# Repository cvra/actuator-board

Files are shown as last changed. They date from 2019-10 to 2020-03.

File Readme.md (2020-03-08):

## CVRA Actuator Board

__Features:__

- STM32F302K8U6 (64K Flash, 16K RAM)
- IOs
    - 1 Digital input
    - 2 Analog input
    - 2 Servo PWM
    - 2 motor outputs for vacuum pump
- CAN interface with two 4pin Molex PicoBlade for daisy chaining
- Debug connector (7pin Molex PicoBlade)
    - SWD
    - UART

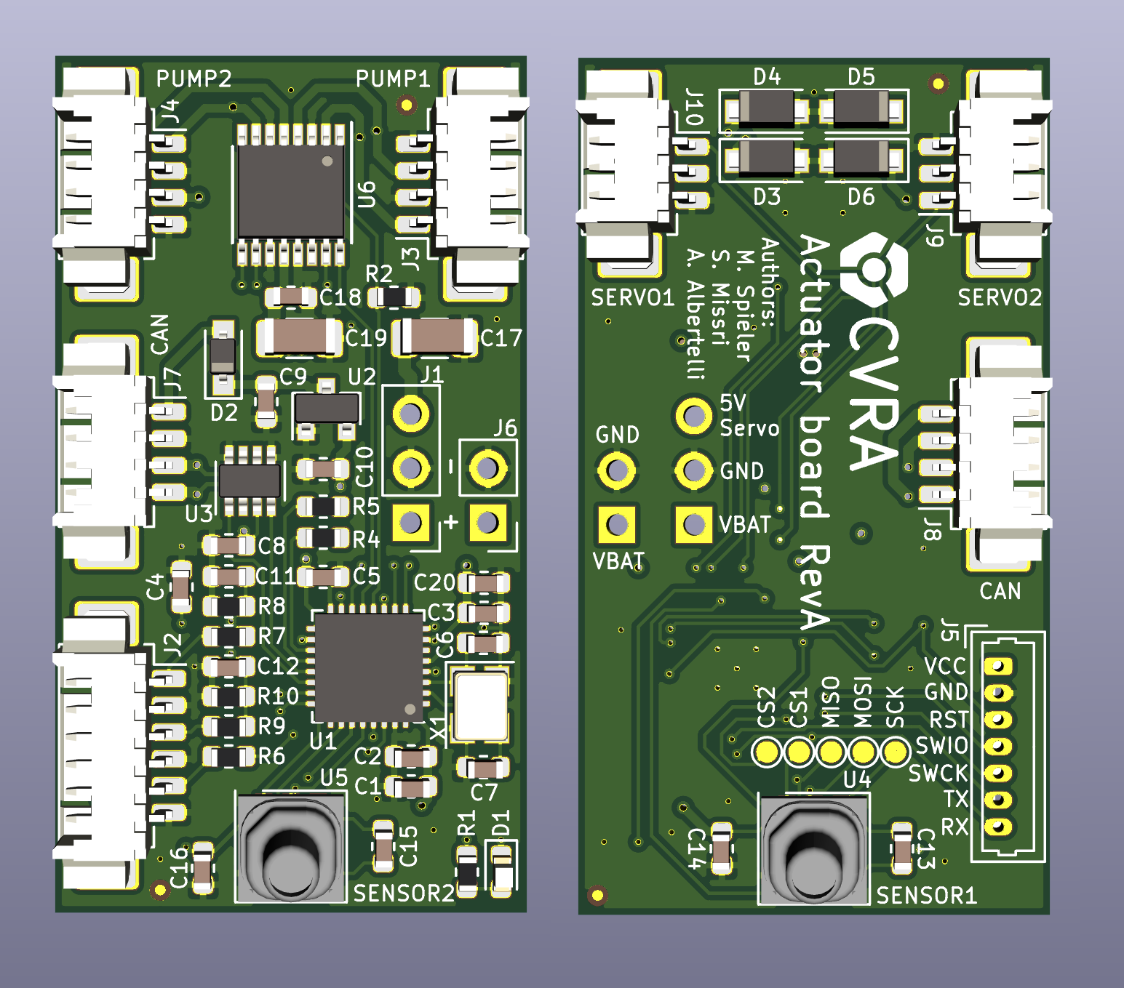
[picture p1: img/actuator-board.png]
Board Rendering

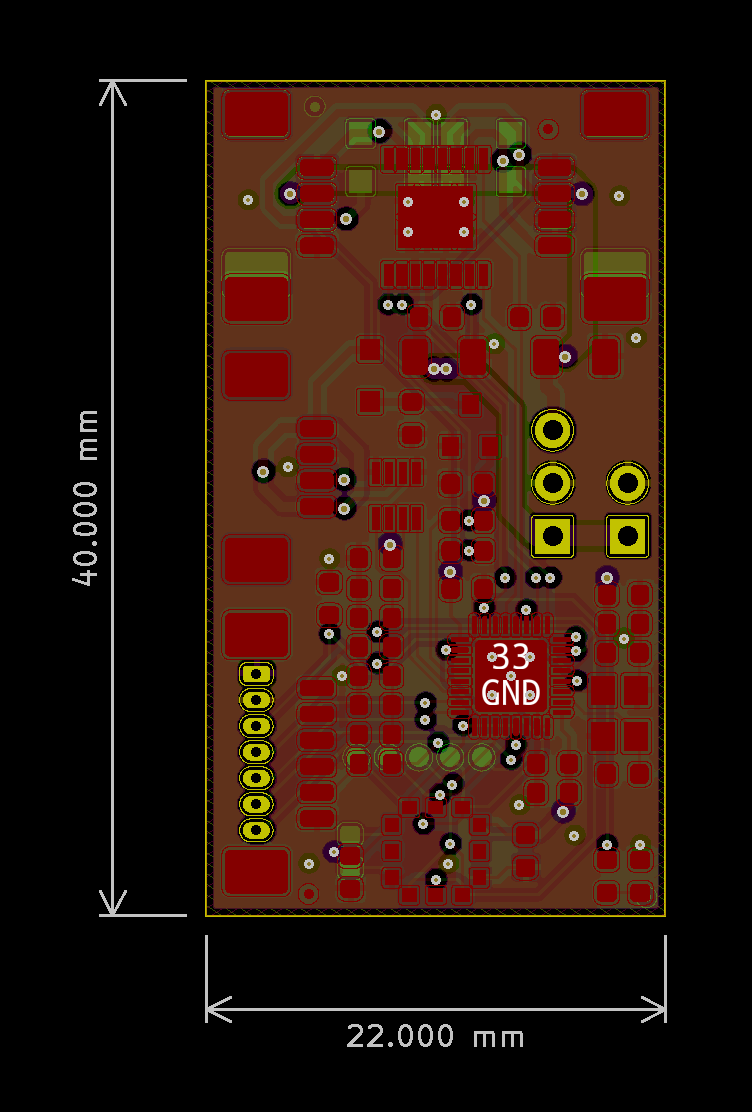
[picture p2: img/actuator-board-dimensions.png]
Board Dimensions


## Generating Digikey BOM using Kicost

Generate the Bom in XML format from KiCAD, then:

```
kicost -i actuator-board.xml --include digikey
```

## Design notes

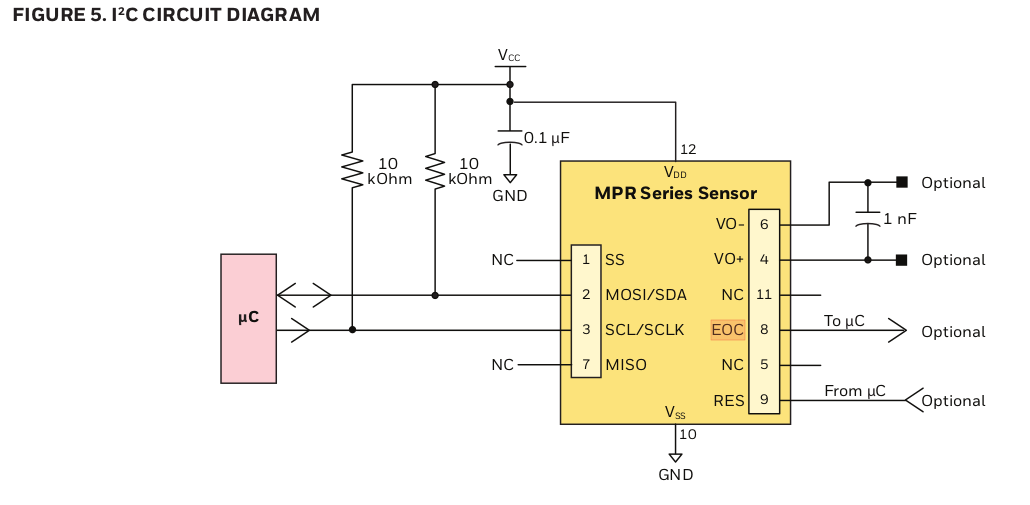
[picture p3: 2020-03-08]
doc/mprls_ref_design.png

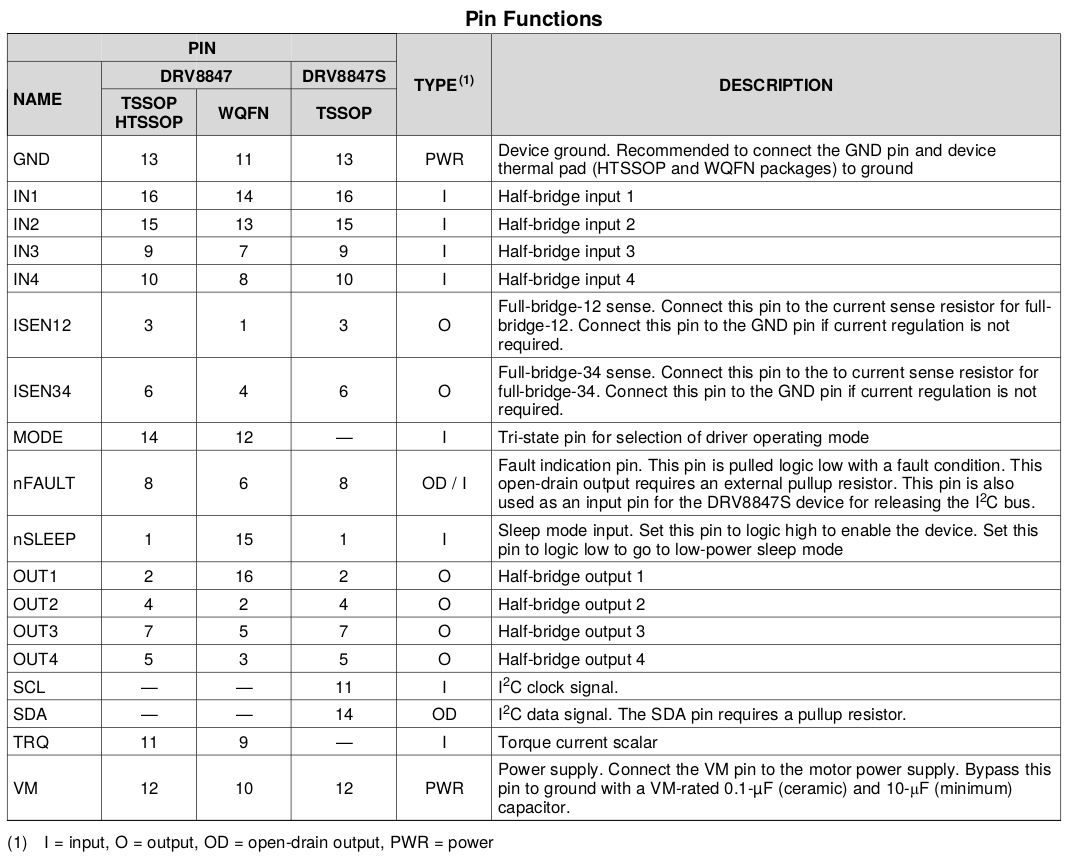
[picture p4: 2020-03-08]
doc/drv8847_pinout.png

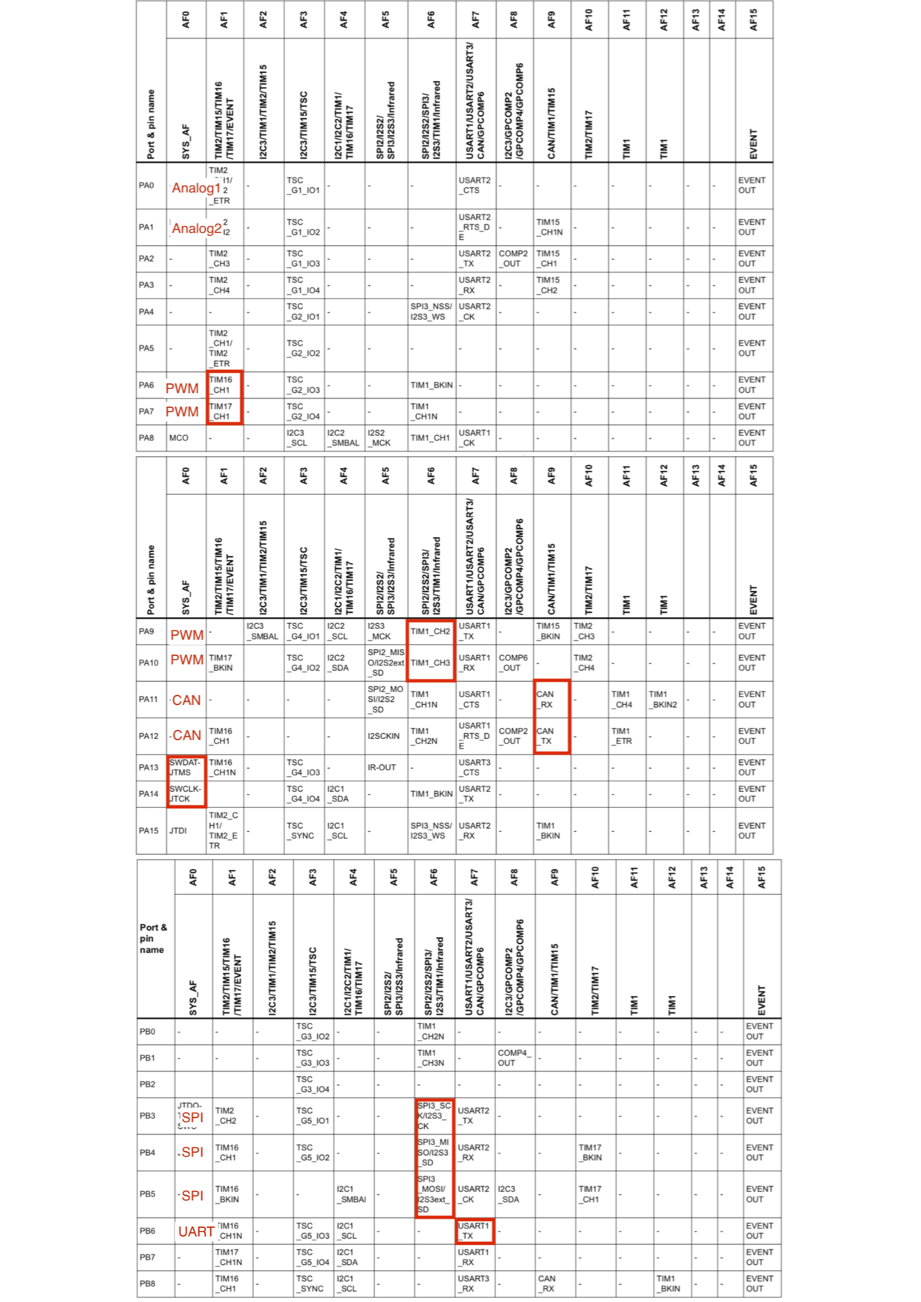
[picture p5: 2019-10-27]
doc/alternate_function.png

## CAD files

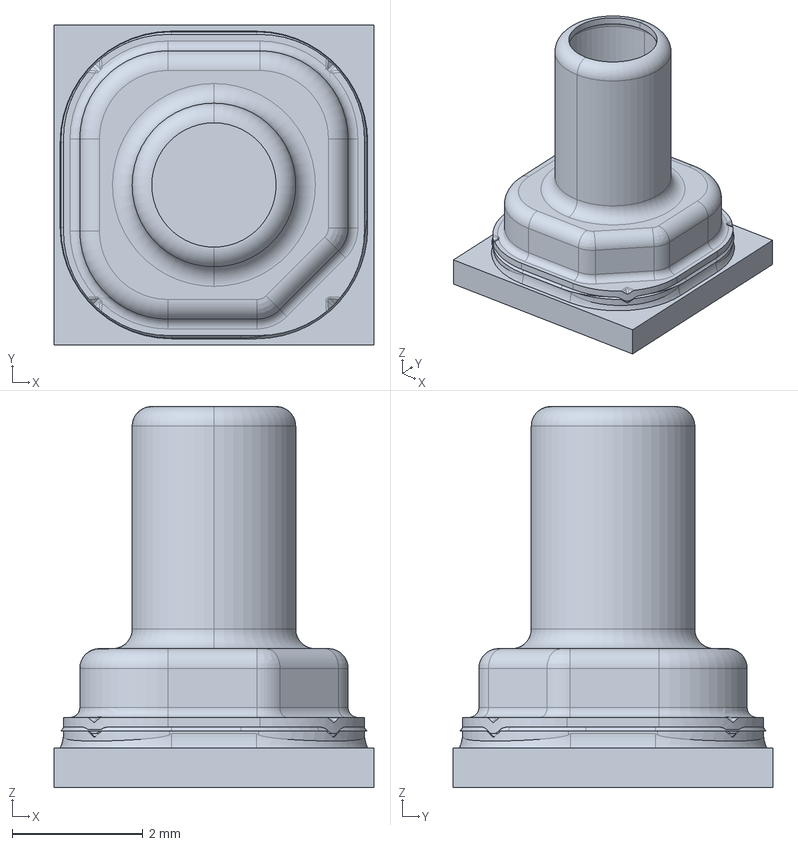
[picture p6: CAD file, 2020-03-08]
3dshapes/MPR.stp
4.89 x 4.89 x 5.82 mm

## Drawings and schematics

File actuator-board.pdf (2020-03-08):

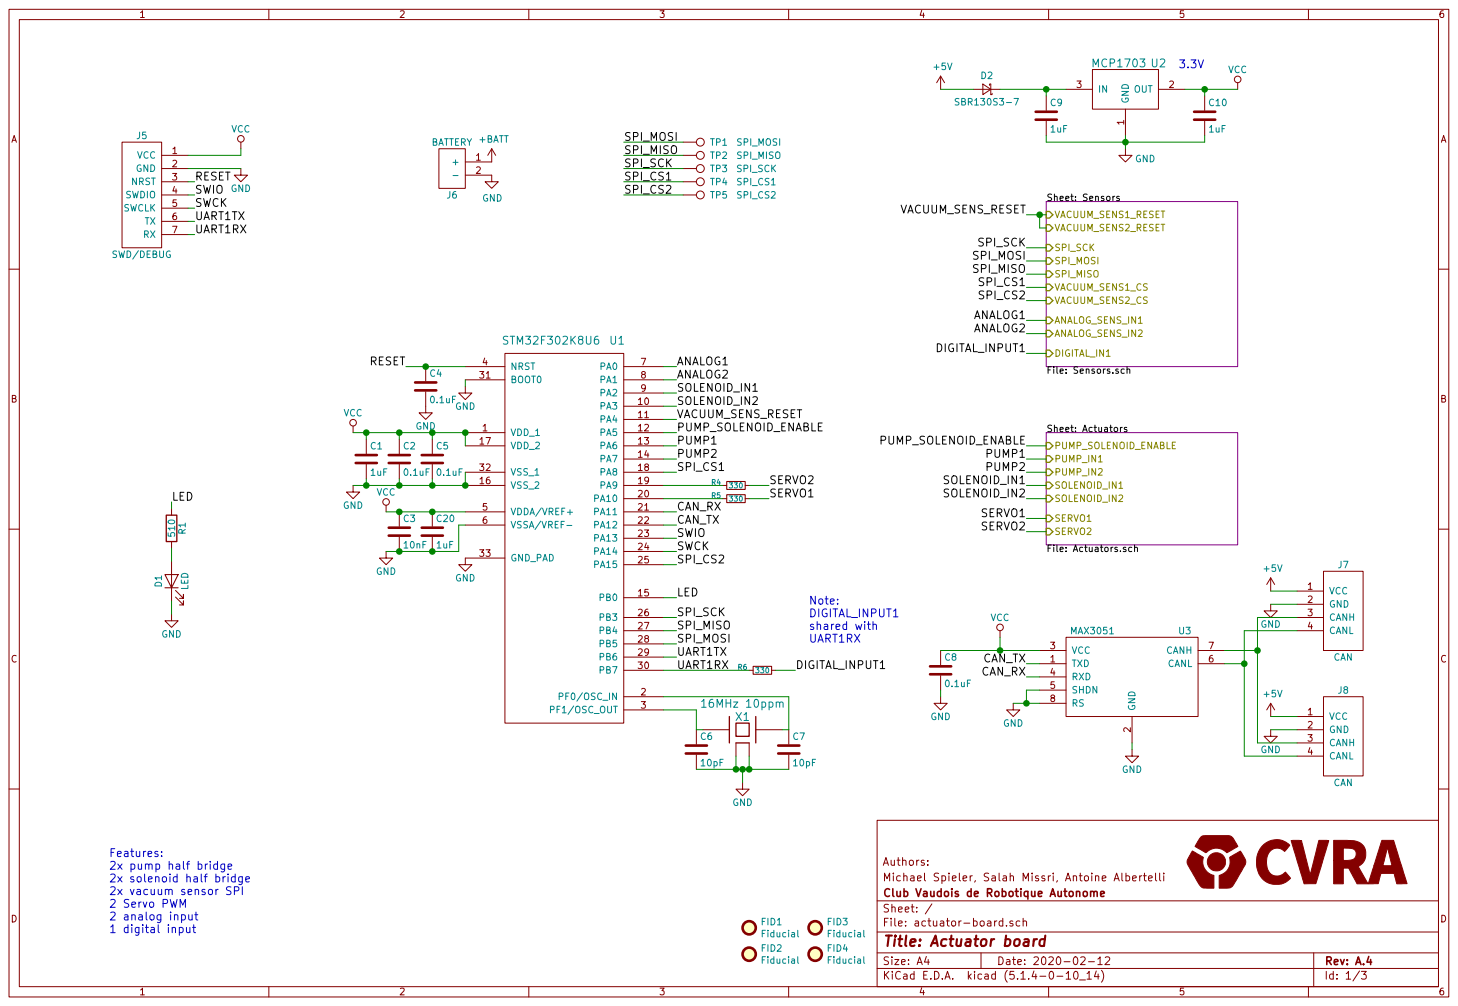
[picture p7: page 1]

SOLENOID_IN1 SOLENOID_IN2 Sheet: Sensors File: Sensors.sch VACUUM_SENS1_RESET ANALOG_SENS_IN1 ANALOG_SENS_IN2 DIGITAL_IN1 VACUUM_SENS2_RESET SPI_SCK

Sheet: Actuators File: Actuators.sch PUMP_IN1 PUMP_IN2 SERVO1 SERVO2 PUMP_SOLENOID_ENABLE

Features: 2x pump half bridge

Michael Spieler, Salah Missri, Antoine Albertelli Authors:

File: actuator-board.sch Sheet: / Club Vaudois de Robotique Autonome

Id: 1/3 Title: Actuator board

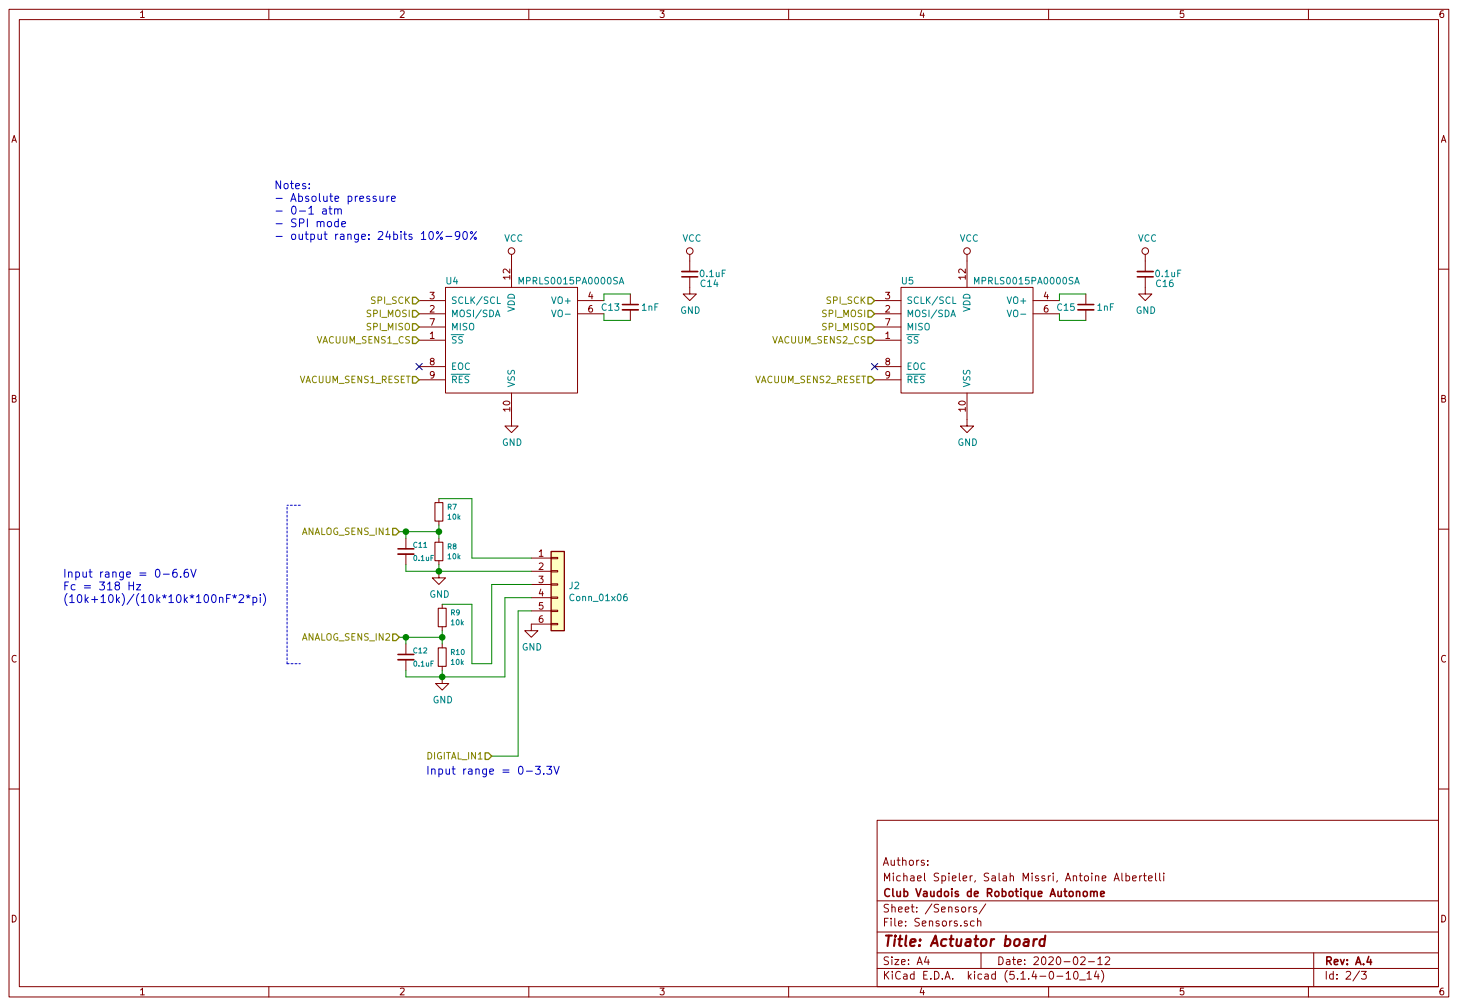
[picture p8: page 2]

File: Sensors.sch Sheet: /Sensors/ Club Vaudois de Robotique Autonome

Id: 2/3 Title: Actuator board

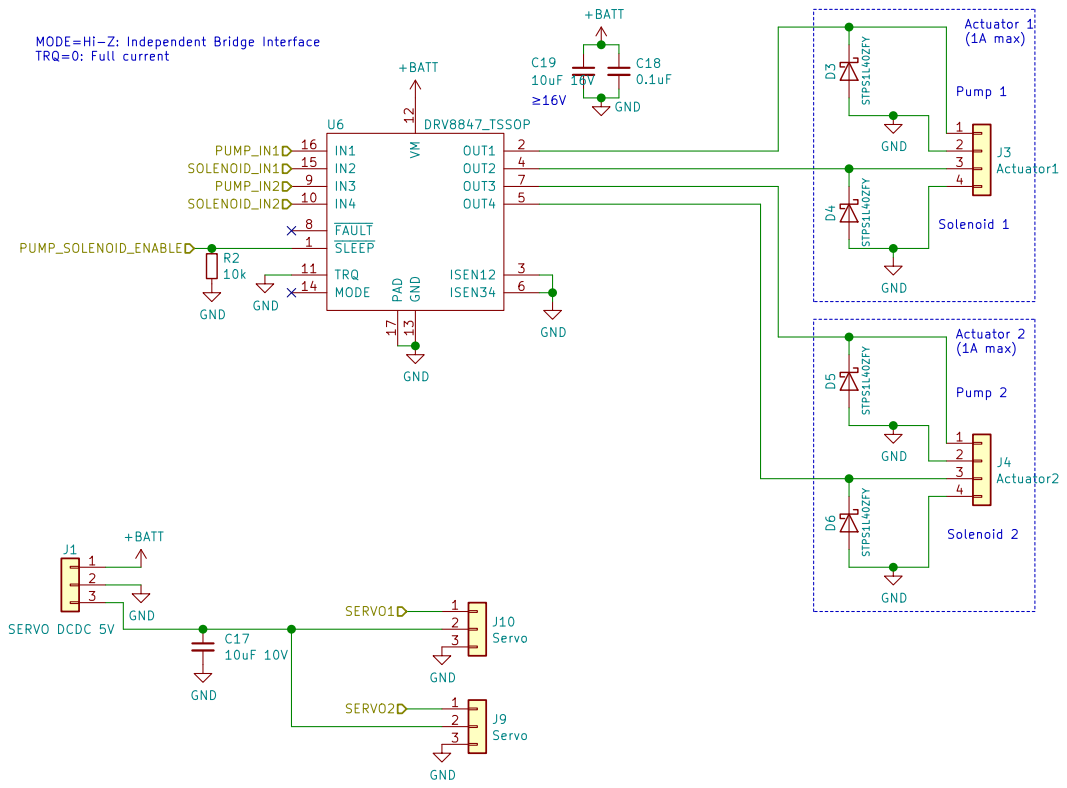
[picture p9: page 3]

File: Actuators.sch Sheet: /Actuators/ Club Vaudois de Robotique Autonome

Id: 3/3 Title: Actuator board

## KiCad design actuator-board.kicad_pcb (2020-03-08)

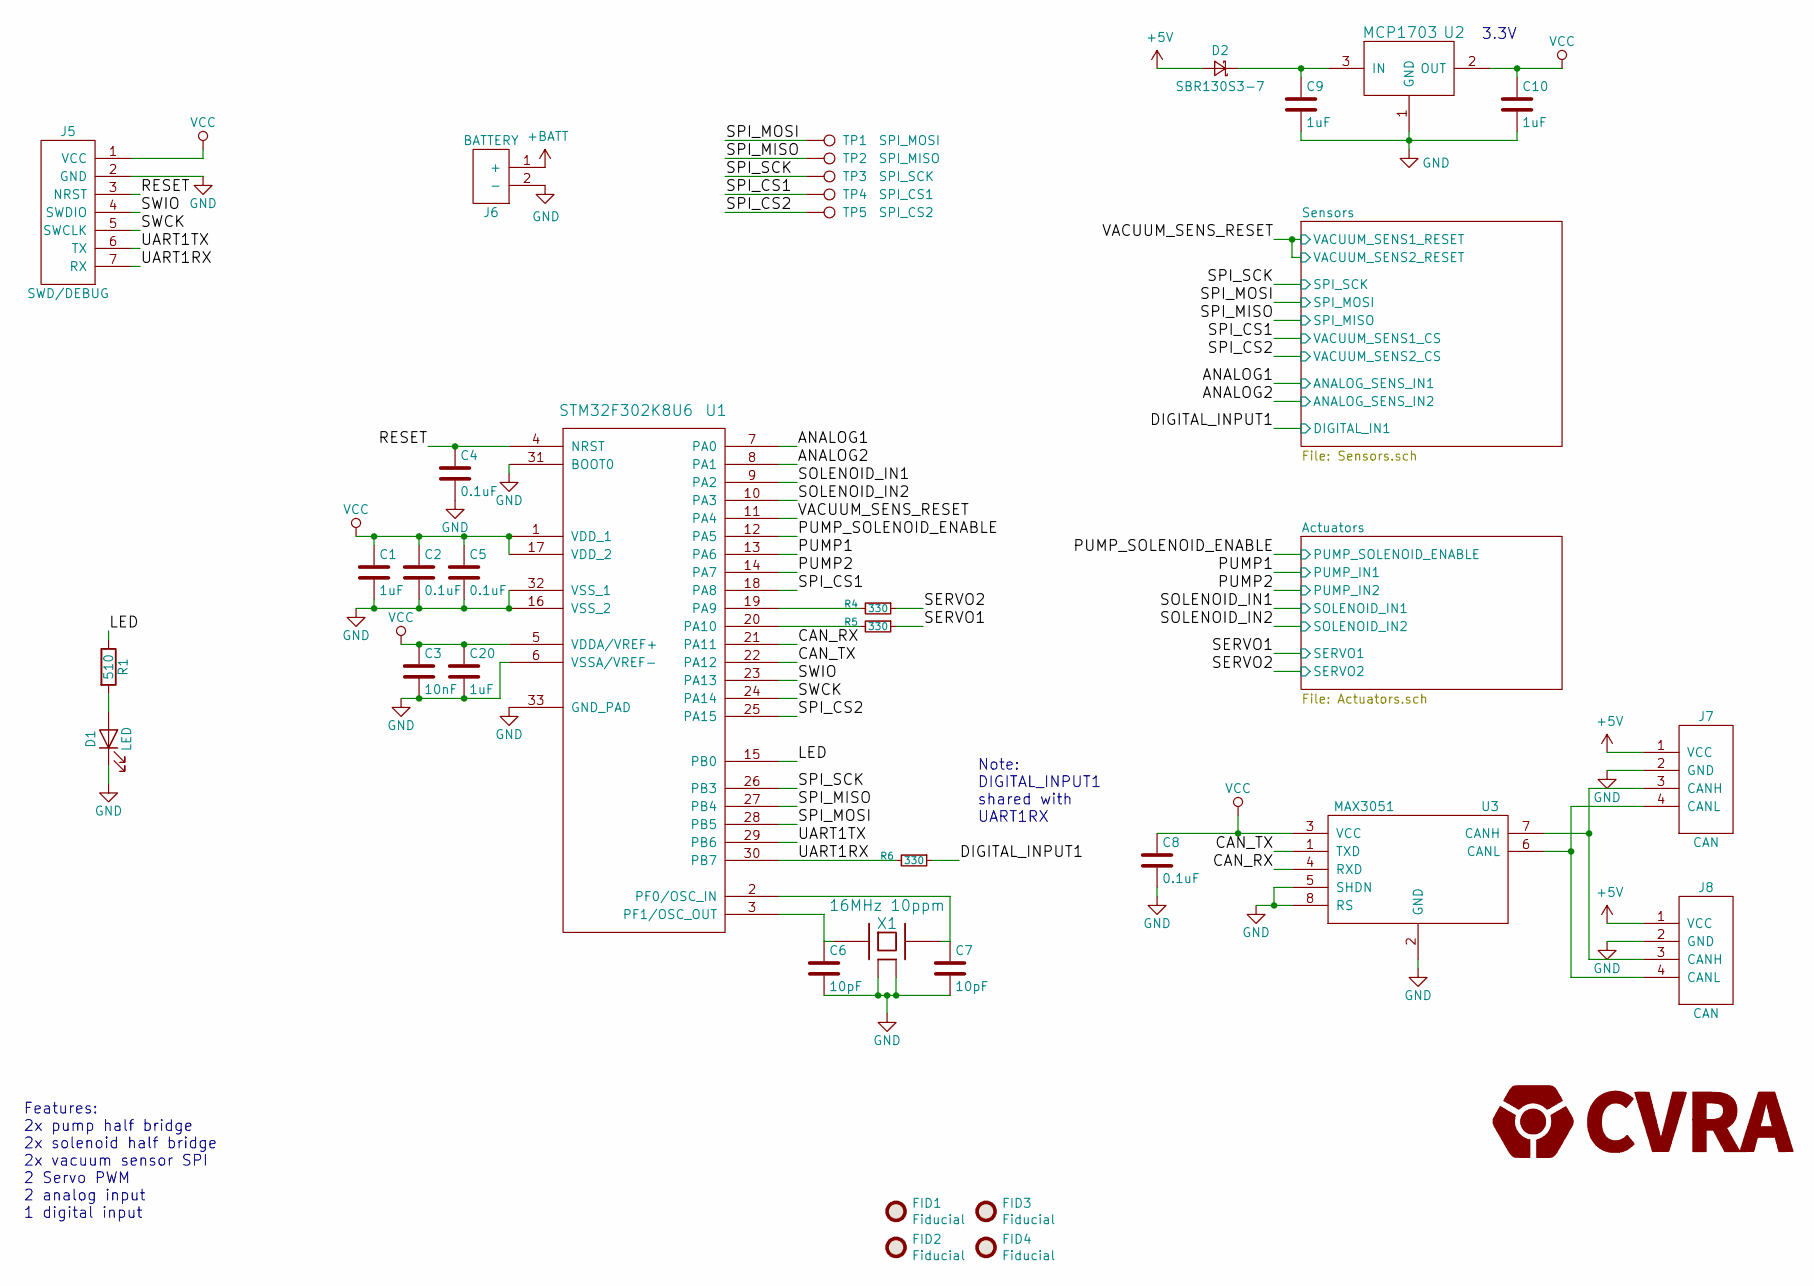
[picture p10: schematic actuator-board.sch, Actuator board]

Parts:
C1, C9, C10, C20: 1uF; C_0603_1608Metric; digikey# 399-3118-1-ND
C2, C4, C5, C8: 0.1uF; C_0603_1608Metric; digikey# 399-1283-1-ND
C3: 10nF; C_0603_1608Metric; digikey# 399-1092-1-ND
C6, C7: 10pF; C_0603_1608Metric; digikey# 399-17563-1-ND
D1: LED; LED_0603_1608Metric; digikey# VLMTG1300-GS08CT-ND
D2: SBR130S3-7; D_SOD-323_HandSoldering; digikey# SBR130S3-7DICT-ND
FID1, FID2, FID3, FID4: Fiducial; Fiducial_0.5mm_Mask1mm
J5: SWD/DEBUG; Molex_PicoBlade_53047-0710_1x07_P1.25mm_Vertical
J6: BATTERY; PinHeader_1x02_P2.54mm_Vertical
J7, J8: CAN; Molex_PicoBlade_53261-0471_1x04-1MP_P1.25mm_Horizontal; digikey# WM7622CT-ND
R1: 510; R_0603_1608Metric; digikey# 311-510GRCT-ND
R4, R5, R6: 330; R_0603_1608Metric; digikey# 311-330HRCT-ND
TP1: SPI_MOSI; TestPoint_Pad_D1.0mm
TP2: SPI_MISO; TestPoint_Pad_D1.0mm
TP3: SPI_SCK; TestPoint_Pad_D1.0mm
TP4: SPI_CS1; TestPoint_Pad_D1.0mm
TP5: SPI_CS2; TestPoint_Pad_D1.0mm
U1: STM32F302K8U6; QFN-32-1EP_5x5mm_P0.5mm_EP3.45x3.45mm; digikey# 497-14700-ND
U2: MCP1703; SOT-23; digikey# MCP1703T-3302E/CBCT-ND
U3: MAX3051; SOT-23-8; digikey# MAX3051EKA+TCT-ND
X1: 16MHz 10ppm; Crystal_SMD_SeikoEpson_TSX3225-4Pin_3.2x2.5mm; digikey# SER4069CT-ND

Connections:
+5V: D2.2 (A), J7.1 (VCC), J8.1 (VCC)
+BATT: J6.1 (+); also elsewhere on the board
/ANALOG1: U1.7 (PA0); also elsewhere on the board
/ANALOG2: U1.8 (PA1); also elsewhere on the board
/CAN_RX: U1.21 (PA11), U3.4 (RXD)
/CAN_TX: U1.22 (PA12), U3.1 (TXD)
/DIGITAL_INPUT1: R6.1; also elsewhere on the board
/LED: R1.1, U1.15 (PB0)
/PUMP1: U1.13 (PA6); also elsewhere on the board
/PUMP2: U1.14 (PA7); also elsewhere on the board
/PUMP_SOLENOID_ENABLE: U1.12 (PA5); also elsewhere on the board
/RESET: C4.1, J5.3 (NRST), U1.4 (NRST)
/SERVO1: R5.1; also elsewhere on the board
/SERVO2: R4.1; also elsewhere on the board
/SOLENOID_IN1: U1.9 (PA2); also elsewhere on the board
/SOLENOID_IN2: U1.10 (PA3); also elsewhere on the board
/SPI_CS1: TP4.1, U1.18 (PA8); also elsewhere on the board
/SPI_CS2: TP5.1, U1.25 (PA15); also elsewhere on the board
/SPI_MISO: TP2.1, U1.27 (PB4); also elsewhere on the board
/SPI_MOSI: TP1.1, U1.28 (PB5); also elsewhere on the board
/SPI_SCK: TP3.1, U1.26 (PB3); also elsewhere on the board
/SWCK: J5.5 (SWCLK), U1.24 (PA14)
/SWIO: J5.4 (SWDIO), U1.23 (PA13)
/UART1RX: J5.7 (RX), R6.2, U1.30 (PB7)
/UART1TX: J5.6 (TX), U1.29 (PB6)
/VACUUM_SENS_RESET: U1.11 (PA4); also elsewhere on the board
GND: C1.2, C2.2, C3.2, C4.2, C5.2, C6.2, C7.2, C8.2, C9.2, C10.2, C20.2, D1.1 (K), J5.2 (GND), J6.2 (-), J7.2 (GND), J8.2 (GND), U1.6 (VSSA/VREF-), U1.16 (VSS_2), U1.31 (BOOT0), U1.32 (VSS_1), U1.33 (GND_PAD), U2.1 (GND), U3.2 (GND), U3.5 (SHDN), U3.8 (RS), X1.2 (case), X1.4 (case); also elsewhere on the board
unnamed: C6.1, U1.3 (PF1/OSC_OUT), X1.1
unnamed: C7.1, U1.2 (PF0/OSC_IN), X1.3
unnamed: C9.1, D2.1 (K), U2.3 (IN)
unnamed: D1.2 (A), R1.2
unnamed: J7.3 (CANH), J8.3 (CANH), U3.7 (CANH)
unnamed: J7.4 (CANL), J8.4 (CANL), U3.6 (CANL)
unnamed: R4.2, U1.19 (PA9)
unnamed: R5.2, U1.20 (PA10)
VCC: C1.1, C2.1, C3.1, C5.1, C8.1, C10.1, C20.1, J5.1 (VCC), U1.1 (VDD_1), U1.5 (VDDA/VREF+), U1.17 (VDD_2), U2.2 (OUT), U3.3 (VCC); also elsewhere on the board

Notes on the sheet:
Features: 2x pump half bridge 2x solenoid half bridge 2x vacuum sensor SPI 2 Servo PWM 2 analog input 1 digital input
3.3V
Note: DIGITAL_INPUT1 shared with UART1RX

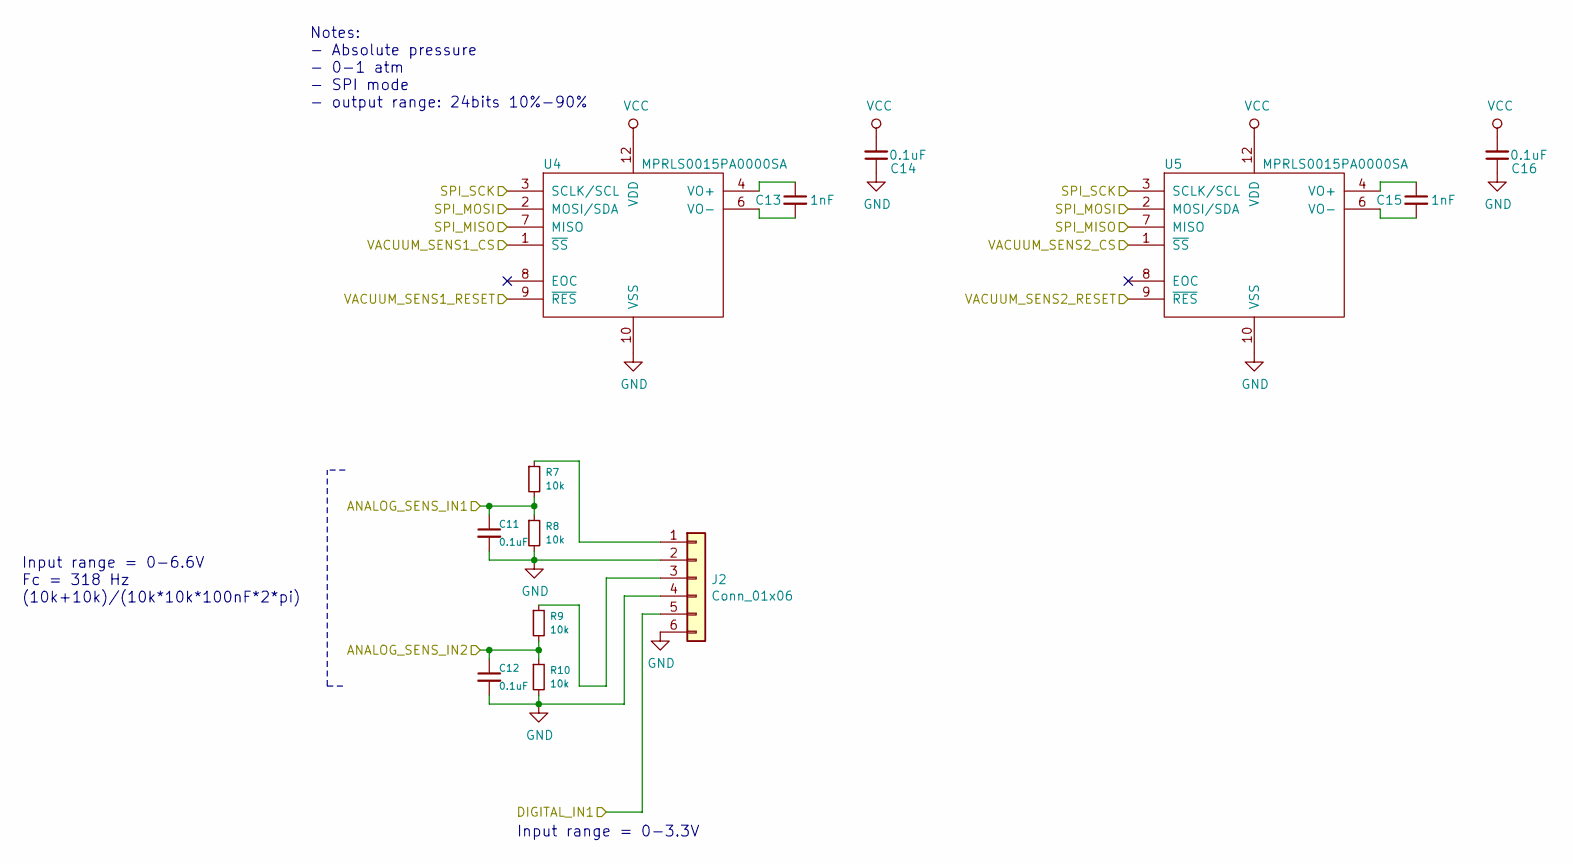
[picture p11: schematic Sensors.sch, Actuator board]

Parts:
C11, C12, C14, C16: 0.1uF; C_0603_1608Metric; digikey# 399-1283-1-ND
C13, C15: 1nF; C_0603_1608Metric; digikey# 399-8984-1-ND
J2: Conn_01x06; Molex_PicoBlade_53261-0671_1x06-1MP_P1.25mm_Horizontal; digikey# WM7626CT-ND
R7, R8, R9, R10: 10k; R_0603_1608Metric; digikey# 311-10KGRCT-ND
U4, U5: MPRLS0015PA0000SA; MPR-AbsoluteRef; digikey# 480-7099-1-ND

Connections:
/ANALOG1: C11.1, R7.2, R8.1; also elsewhere on the board
/ANALOG2: C12.1, R9.2, R10.1; also elsewhere on the board
/DIGITAL_INPUT1: J2.5; also elsewhere on the board
/SPI_CS1: U4.1 (~SS); also elsewhere on the board
/SPI_CS2: U5.1 (~SS); also elsewhere on the board
/SPI_MISO: U4.7 (MISO), U5.7 (MISO); also elsewhere on the board
/SPI_MOSI: U4.2 (MOSI/SDA), U5.2 (MOSI/SDA); also elsewhere on the board
/SPI_SCK: U4.3 (SCLK/SCL), U5.3 (SCLK/SCL); also elsewhere on the board
/VACUUM_SENS_RESET: U4.9 (~RES), U5.9 (~RES); also elsewhere on the board
GND: C11.2, C12.2, C14.1, C16.1, J2.2, J2.4, J2.6, R8.2, R10.2, U4.10 (VSS), U5.10 (VSS); also elsewhere on the board
unnamed: C13.1, U4.4 (VO+)
unnamed: C13.2, U4.6 (VO-)
unnamed: C15.1, U5.4 (VO+)
unnamed: C15.2, U5.6 (VO-)
unnamed: J2.1, R7.1
unnamed: J2.3, R9.1
VCC: C14.2, C16.2, U4.12 (VDD), U5.12 (VDD); also elsewhere on the board

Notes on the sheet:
Notes: - Absolute pressure - 0-1 atm - SPI mode - output range: 24bits 10%-90%
Input range = 0-6.6V Fc = 318 Hz (10k+10k)/(10k*10k*100nF*2*pi)
Input range = 0-3.3V

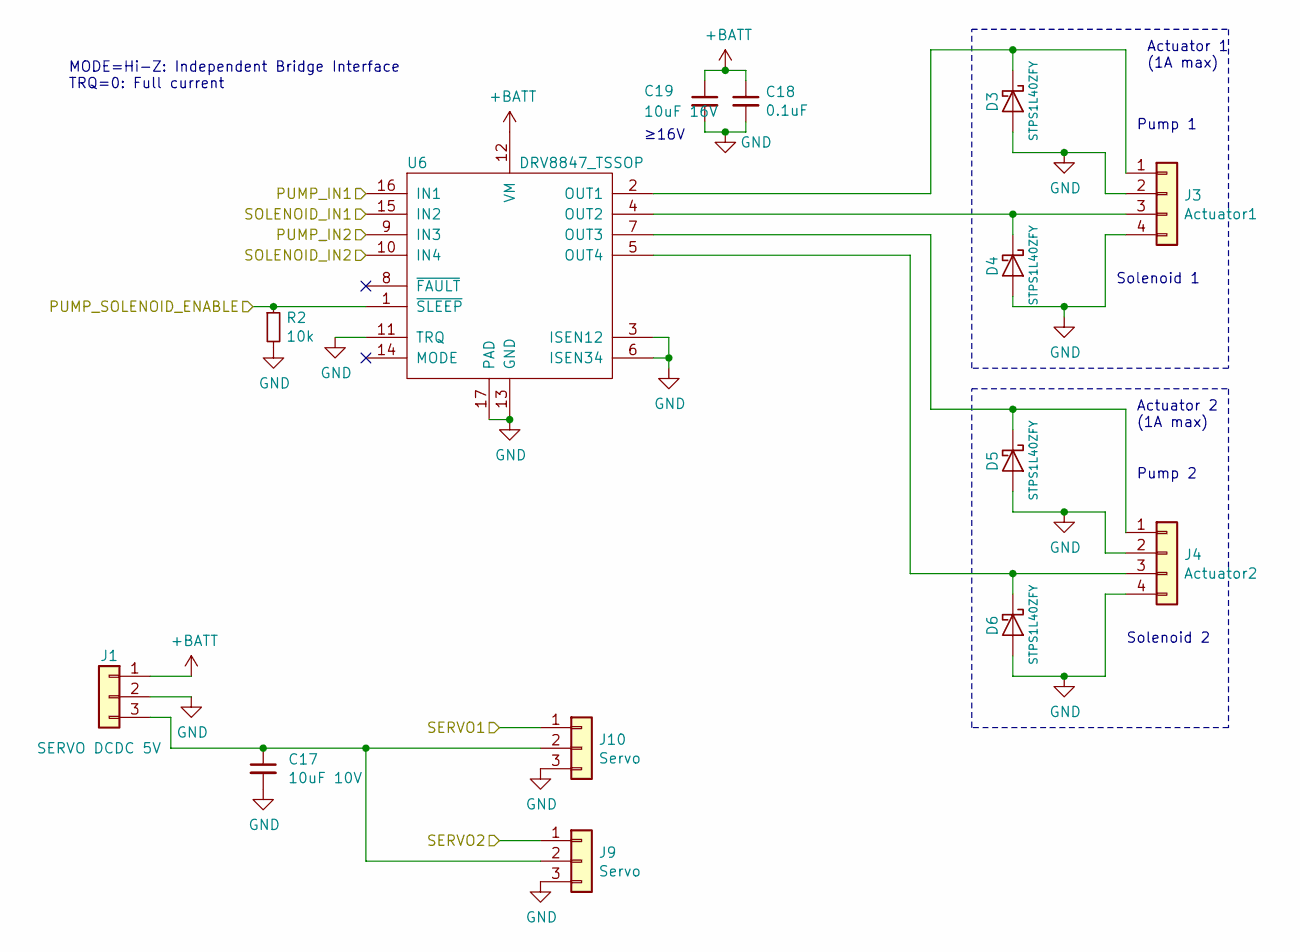
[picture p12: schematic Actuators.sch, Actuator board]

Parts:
C17: 10uF 10V; C_1206_3216Metric; digikey# 399-8155-1-ND
C18: 0.1uF; C_0603_1608Metric; digikey# 399-1283-1-ND
C19: 10uF 16V; C_1206_3216Metric; digikey# 399-7442-1-ND
D3, D4, D5, D6: STPS1L40ZFY; D_SOD-123F; digikey# 497-17153-1-ND
J1: SERVO DCDC 5V; PinHeader_1x03_P2.54mm_Vertical
J3: Actuator1; Molex_PicoBlade_53261-0471_1x04-1MP_P1.25mm_Horizontal; digikey# WM7622CT-ND
J4: Actuator2; Molex_PicoBlade_53261-0471_1x04-1MP_P1.25mm_Horizontal; digikey# WM7622CT-ND
J9, J10: Servo; Molex_PicoBlade_53261-0371_1x03-1MP_P1.25mm_Horizontal; digikey# WM7621CT-ND
R2: 10k; R_0603_1608Metric; digikey# 311-10KGRCT-ND
U6: DRV8847_TSSOP; TSSOP-16-1EP_4.4x5mm_P0.65mm; digikey# 296-53424-1-ND

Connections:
+BATT: C18.1, C19.1, J1.1, U6.12 (VM); also elsewhere on the board
/PUMP1: U6.16 (IN1); also elsewhere on the board
/PUMP2: U6.9 (IN3); also elsewhere on the board
/PUMP_SOLENOID_ENABLE: R2.1, U6.1 (~SLEEP); also elsewhere on the board
/SERVO1: J10.1; also elsewhere on the board
/SERVO2: J9.1; also elsewhere on the board
/SOLENOID_IN1: U6.15 (IN2); also elsewhere on the board
/SOLENOID_IN2: U6.10 (IN4); also elsewhere on the board
GND: C17.2, C18.2, C19.2, D3.2 (A), D4.2 (A), D5.2 (A), D6.2 (A), J1.2, J3.2, J3.4, J4.2, J4.4, J9.3, J10.3, R2.2, U6.3 (ISEN12), U6.6 (ISEN34), U6.11 (TRQ), U6.13 (GND), U6.17 (PAD); also elsewhere on the board
unnamed: C17.1, J1.3, J9.2, J10.2
unnamed: D3.1 (K), J3.1, U6.2 (OUT1)
unnamed: D4.1 (K), J3.3, U6.4 (OUT2)
unnamed: D5.1 (K), J4.1, U6.7 (OUT3)
unnamed: D6.1 (K), J4.3, U6.5 (OUT4)

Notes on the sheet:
Actuator 1 (1A max)
Actuator 2 (1A max)
MODE=Hi-Z: Independent Bridge Interface TRQ=0: Full current
≥16V
Pump 2
Solenoid 2
Solenoid 1
Pump 1

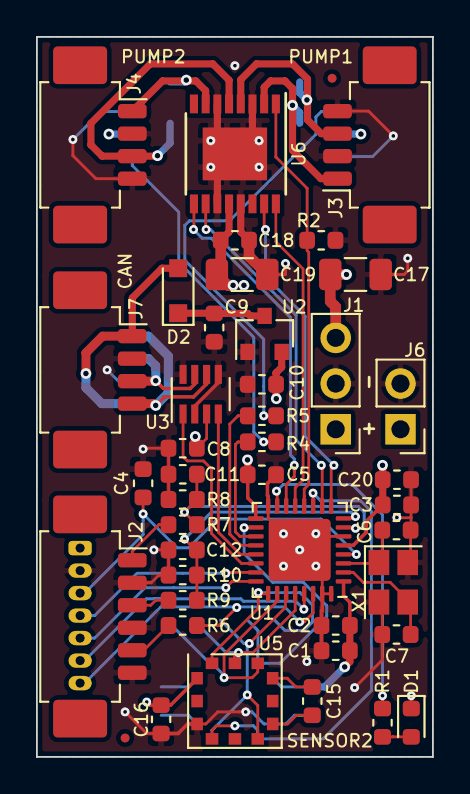
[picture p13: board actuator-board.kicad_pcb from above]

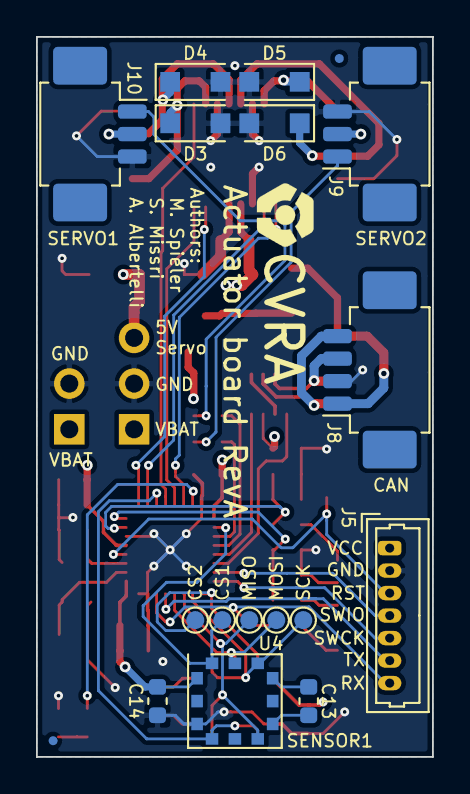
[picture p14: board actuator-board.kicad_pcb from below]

Board: 4 copper layers, 22.0 x 40.0 mm, 62 parts (19 on the bottom side), 47 nets.

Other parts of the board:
G1: LOGO; CVRA-logo-small

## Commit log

2016-03-09 schematic & component placement
    [can-io-board.kicad_pcb, can-io-board.sch]
2016-03-09 pcb rules
    [can-io-board.kicad_pcb]
2016-03-10 routing done
    [can-io-board.kicad_pcb, can-io-board.sch]
2016-03-10 add pdf schematic
2016-03-10 Set GND pad clearance and width
    [can-io-board.kicad_pcb]
2016-03-10 Hide component references in silkscreen
    [can-io-board.kicad_pcb]
2016-03-10 Improve VCC routing
    [can-io-board.kicad_pcb]
2016-03-10 Flip debug connector
    [can-io-board.kicad_pcb]
2016-03-10 nicer tracks
    [can-io-board.kicad_pcb]
2016-03-10 Improve GND connection
    [can-io-board.kicad_pcb]
2016-03-10 Remove silkscreen
    [can-io-board.kicad_pcb]
2016-03-10 add gerber
    [can-io-board-B.Cu.gbl, can-io-board-B.Paste.gbp, can-io-board-B.SilkS.gbo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]
2016-03-10 fix pin name, add silkscreen
    [can-io-board.kicad_pcb, can-io-board.sch]
2016-03-10 add final gerber
    [can-io-board-B.Cu.gbl, can-io-board-B.Mask.gbs, can-io-board-B.SilkS.gbo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]
2016-03-10 track fp lib table
2016-03-10 optimize C9 connection
    [can-io-board-B.Cu.gbl, can-io-board-B.Mask.gbs, can-io-board-B.Paste.gbp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]
2016-03-11 add pcb preview
2016-03-27 oscillator reference
    [can-io-board.sch]
2018-10-17 Start layout on RevB
    [can-io-board.kicad_pcb, can-io-board.sch]
2018-10-17 CAN connector on opposite sides
    [can-io-board.kicad_pcb]
2018-10-18 Reduced number of IO, use PicoBlade connector
    [can-io-board.kicad_pcb, can-io-board.sch]
2018-10-19 Routing almost finished
    [can-io-board.kicad_pcb, can-io-board.sch]
2018-10-19 fix DRC
    [can-io-board.kicad_pcb]
2018-10-19 Capacitor spacing
    [can-io-board.kicad_pcb]
2018-10-24 Improved GND connection, solder mask clearance
    [can-io-board.kicad_pcb]
2018-10-25 Silkscreen placement
    [can-io-board.kicad_pcb, can-io-board.sch]
2018-10-25 Add Digikey ref in schematic, add BOM
    [bom.csv, can-io-board.sch]
2018-10-28 Add CAN reverse voltage protection diode
    [bom.csv, can-io-board.kicad_pcb, can-io-board.sch]
2018-10-28 Plot schematic, move RevA to subfolder
    [can-io-board-B.Cu.gbl, can-io-board-B.Mask.gbs, can-io-board-B.Paste.gbp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]
2018-10-28 Solder paste clearance -10%
    [can-io-board.kicad_pcb]
2018-10-28 Gerber file export
    [can-io-board-B.Cu.gbl, can-io-board-B.Mask.gbs, can-io-board-B.Paste.gbp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]
2019-10-25 Start actuator-board
    [actuator-board.sch, bom.csv, can-io-board.kicad_pcb]
2019-10-25 remove CAN-IO stuff
    [can-io-board-B.Cu.gbl, can-io-board-B.Mask.gbs, can-io-board-B.Paste.gbp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]
2019-10-26 pin assignment WIP
    [actuator-board.sch]
2020-01-18 Ignore kicad backups and PDFs
2020-01-18 Add components for half bridges and vaccuum sensor
2020-01-18 Finish the design of th actuator board schematic
    [Actuators.sch, Sensors.sch, actuator-board.sch]
2020-01-25 Correct schematics after review
    [Actuators.sch, Sensors.sch, actuator-board.sch]
2020-02-02 Cleanup labels, motor placement, power labels
    [Actuators.sch, Sensors.sch, actuator-board.sch]
2020-02-02 Change to Schottky flyback diode, update valve symbol
    [Actuators.sch, actuator-board.sch]
2020-02-02 Clear component annotation
    [Actuators.sch, Sensors.sch, actuator-board.sch]
2020-02-06 updated kicad lib symbols
2020-02-06 Switch to SPI, fixed sensor and motor driver symbols.
    [Actuators.sch, Sensors.sch, actuator-board.sch]
2020-02-08 Work on footprint assignment
    [Actuators.sch, Sensors.sch, actuator-board.sch]
2020-02-12 Review update
    [Actuators.sch, Sensors.sch, actuator-board.sch]
2020-02-12 Input range note, rough footprint assignment
    [Actuators.sch, Sensors.sch, actuator-board.sch]
2020-02-12 Create PCB file, import footprints, rough arrangement
    [actuator-board.kicad_pcb]
2020-02-13 Upadate footprints, rough arrangement
    [Actuators.sch, Sensors.sch, actuator-board.kicad_pcb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]
2020-02-13 Add digikey references for BOM
    [Actuators.sch, Sensors.sch, actuator-board.sch]
2020-02-13 Rough component placement, defined outline
    [actuator-board.kicad_pcb]
2020-02-16 Update footprints, better refdes, cleanup schematic, 40x22mm outline
    [Actuators.sch, Sensors.sch, actuator-board.kicad_pcb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]
2020-02-16 Update authors, DRC rules, layers, track/via settings
    [Actuators.sch, Sensors.sch, actuator-board.kicad_pcb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]
2020-02-20 Sensor/gpio/debug routing
    [actuator-board.kicad_pcb]
2020-02-20 Refdes silkscreen text size 1mm -> 0.7mm
    [actuator-board.kicad_pcb]
2020-02-22 layout: CAN, rearrange LED/CS1/CS2
    [actuator-board.kicad_pcb, actuator-board.sch]
2020-02-22 layout: power electronics, more components on F.Cu layer
    [actuator-board.kicad_pcb, actuator-board.sch]
2020-02-23 HTSSOP motor driver, component arrangment, added MCU capacitor
    [Actuators.sch, actuator-board.kicad_pcb, actuator-board.sch]
2020-02-23 Silk screen doc, ground vias, exchange servo 1 <-> 2
    [Actuators.sch, actuator-board.kicad_pcb, actuator-board.sch]
2020-03-01 Changes from review: move C2, move VCC via, add fiducials, component placement
    [actuator-board.kicad_pcb, actuator-board.sch]
2020-03-01 PDF schematic
2020-03-01 Gerber files
    [actuator-board-B_Cu.gbl, actuator-board-B_Mask.gbs, actuator-board-B_Paste.gbp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]
2020-03-08 Update DigiKey references
    [Actuators.sch, Sensors.sch, actuator-board.sch]
2020-03-08 Add pressure sensor 3D shape
    [MPR.stp, actuator-board.kicad_pcb]
2020-03-08 Update README and board rendering
